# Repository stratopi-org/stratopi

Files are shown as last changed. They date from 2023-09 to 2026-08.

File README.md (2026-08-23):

# StratoPi 🎈 👽 🛸

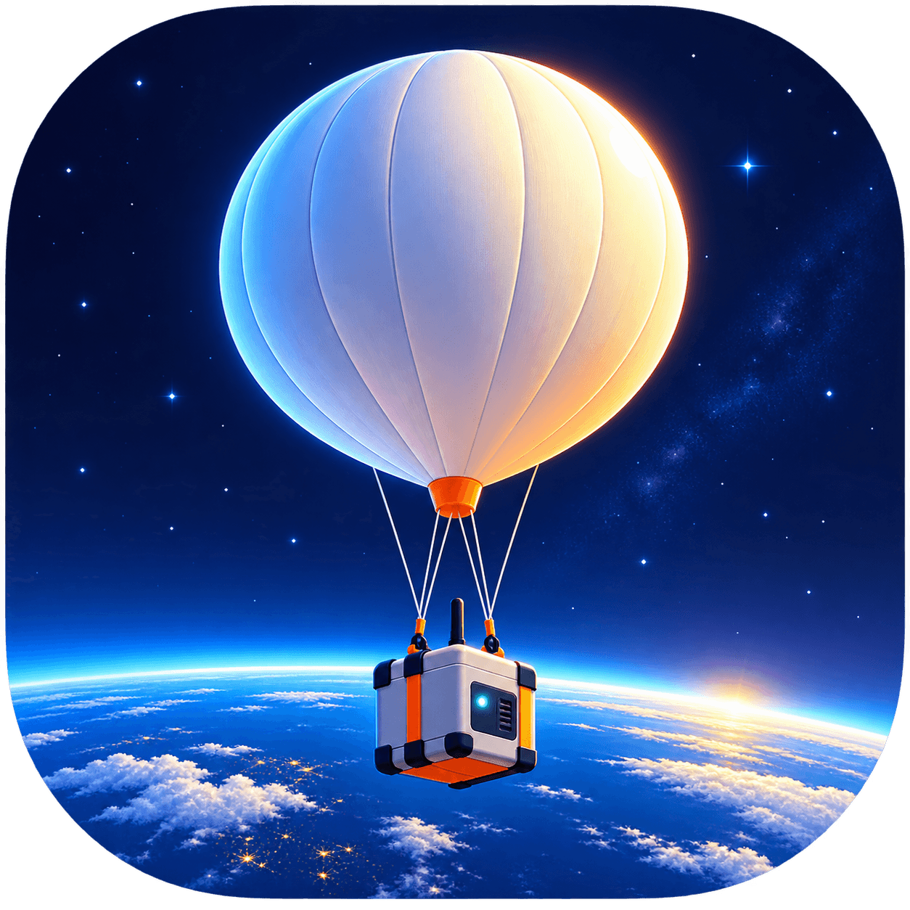
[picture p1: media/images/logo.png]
StratoPi


## Goal

The goal is to launch a latex weather balloon filled with helium into the stratosphere while recording the entire video footage of the ascent and descent flights using multiple cameras. Successfully recover the payload, which includes the Raspberry Pi computer, flight data _(date, GPS, temperature, pressure, humidity, etc)_, and video cameras and footage. If you like computing, Raspberry Pi's, space, flight, and have way too much free time, this might just be the project for you.

- Altitude goal is 100,000ft _(30,480m)_.

Open sourced and community developed. StratoPi is 100% purely a hobby project with zero financial incentives. All parts purchased at retail prices. My experience is mostly as the founder of [Elastic Byte](https://elasticbyte.net) and a DevOps Engineer so this is definitely uncharted territory for me personally.

## Parts

View the [parts list](https://github.com/stratopi-org/stratopi/blob/master/PARTS.md).

## Legality / FAA

According to the [Strato Flights website](https://www.stratoflights.com/en/tutorial/weather-balloon-registration-insurance/usa/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,FAA%20Part%20101), must have approval from the Federal Aviation Administration _(FAA)_. _Laws and regulations may undergo significant changes at any time due to ongoing developments involving spy balloons._

See:

- https://eclipse.montana.edu/education/engineering-course/eng-lesson09-faaregs.pdf
- https://www.ecfr.gov/current/title-14/chapter-I/subchapter-F/part-101
- https://www.ecfr.gov/current/title-14/chapter-I/subchapter-C/part-48
- https://www.cbsnews.com/news/military-tracking-balloon-western-us-military/

## Media

Raspberry Pi computer, battery, communications payload overview (http://www.youtube.com/watch?v=SpzycIWPKsQ "Raspberry Pi computer, battery, communications payload overview")

RunCam 5 Camera Unboxing (http://www.youtube.com/watch?v=Ua4CM7kJQfI "RunCam 5 Camera Unboxing")

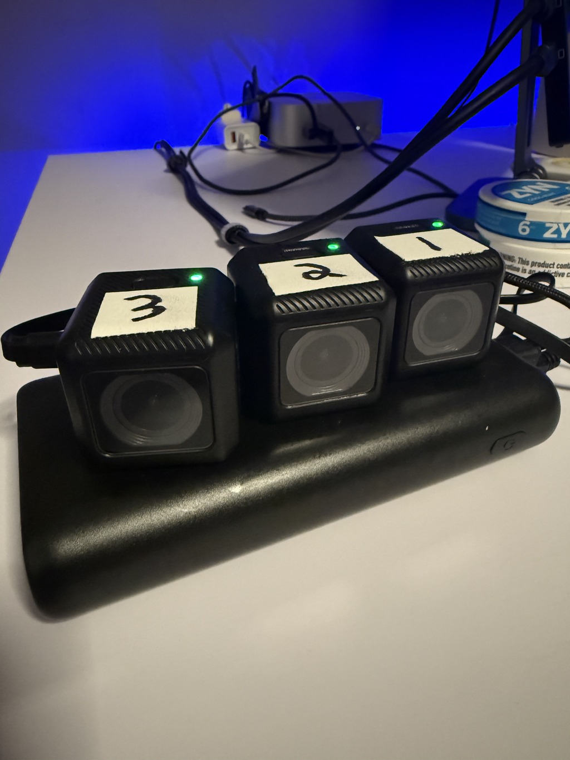
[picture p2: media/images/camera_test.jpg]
RunCam 5 Camera Power Test


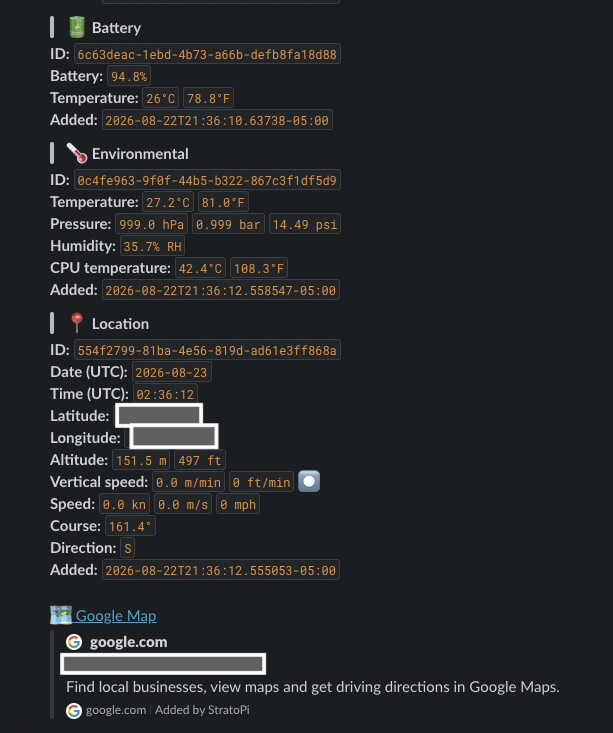
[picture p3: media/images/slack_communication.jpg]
Slack Communication


## Software architecture

All the software is written in Python 3 using standard PyPI packages. The pattern of each application is essentially poll for some data, and then insert that data into PostgreSQL. The exception being the communication application which listens for data from PostgreSQL via `pg_notify` and sends it to Slack via cellular networks. Originally, I was planning to run each application in a Docker container but decided to keep things as simple as possible and opted to use tried and true _systemd_ services for each application. [KISS](https://en.wikipedia.org/wiki/KISS_principle)!

- ### [battery](https://github.com/stratopi-org/stratopi/tree/master/software/battery)

Polls the battery percentage as well as the battery temperature and inserts the data into PostgreSQL.

- ### [communication](https://github.com/stratopi-org/stratopi/tree/master/software/communication)

Listens for battery, environmental, and location data from PostgreSQL via `pg_notify` and sends it to Slack via cellular networks.

- ### [environmental](https://github.com/stratopi-org/stratopi/tree/master/software/environmental)

Polls the Bosch BME280 sensor, Raspberry Pi CPU temperature, and inserts the data into PostgreSQL. Provides temperature, atmospheric pressure, and humidity.

- ### [location](https://github.com/stratopi-org/stratopi/tree/master/software/location)

Polls the Waveshare GPS and inserts the data into PostgreSQL. Provides date, time, latitude, longitude, altitude, speed, and course. From course, can also determine direction such as North, Southeast, etc. Addditionally vertical speed per minute is automatically calculated via a PostgreSQL trigger _(see [code](https://github.com/stratopi-org/stratopi/blob/master/software/location/database-schema.sql#L45))_.

## Tests

View [various tests](https://github.com/stratopi-org/stratopi/blob/master/docs/tests.md) _(camera, mass, power, etc)_.

## Wanna help?

- See [GitHub Issues](https://github.com/stratopi-org/stratopi/issues?q=is%3Aopen+is%3Aissue+label%3Aenhancement) for outstanding tasks
- Potentially joining the launch and recovery in person _(Tennessee launch...)_
- Code review and PR's of my _noob_ Python 🙈. Dig into the [software](https://github.com/stratopi-org/stratopi/tree/master/software).
- Parts recommendations and optimizations
- 3d modeling and printing _(structural and mounting aspects)_
- Website / Github Pages
- Flight, space, physics experience as I am sure I am negligently overlooking details
- GIS and GPS experience. KML, GeoJSON, GPS Visualizer, Google Earth/Maps
- Video editing of the flight footage 🤞
- Have a latex baloon "hookup"?
- Have a helium "hookup"? 😉

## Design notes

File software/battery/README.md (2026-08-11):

# battery

## Create PostgreSQL Schema

```shell
sudo -u postgres psql -h 127.0.0.1 -d stratopi -U stratopi -f ./database-schema.sql --password
```

## Install systemd Service

```shell
./install.sh
```

## Environment Variables

- `LOG_LEVEL` _(default=INFO)_
- `POSTGRES_URL` _(required)_

## View Logs

```shell
./logs.sh [--follow]
```

## Utilities

- Create a PostgreSQL `pg_dump` backup of battery data:

```shell
python -m util.backup
```

- Truncate all battery data from PostgreSQL:

```shell
python -m util.truncate
```

## Pip

- `pip-outdated` checks if any PyPI packages are outdated.

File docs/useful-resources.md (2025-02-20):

# Documentation and resources

- [National Weather Service Weather Balloon / Upper Air Observations](https://www.weather.gov/rev/upperair)
- [Weather Balloon Tutorial](https://www.stratoflights.com/en/tutorial/)
- [UK High Altitude Society](https://www.ukhas.org.uk/doku.php?id=start)
- [FAA Regulations for Unmanned Free Balloons](https://eclipse.montana.edu/education/engineering-course/eng-lesson09-faaregs.pdf)
- [Nationwide Eclipse Ballooning Project](https://eclipse.montana.edu/)
- [PiSugar 3 Wiki](https://github.com/PiSugar/PiSugar/wiki/PiSugar-3-Series)
- [Waveshark SIM7600E-H 4G HAT product page](https://www.waveshare.com/wiki/SIM7600E-H_4G_HAT)
- [Core Electronics - 4G and GPS HAT For Raspberry Pi - Waveshare SIM7600X](https://core-electronics.com.au/guides/raspberry-pi-4g-gps-hat/)
- [Raspberry Pi Weather Station (video)](https://www.youtube.com/watch?v=ChQpD2gsC20&ab_channel=ExplainingComputers)
- [Humidity, temperature and pressure project on RaspberryPi](https://projects.raspberrypi.org/en/projects/build-your-own-weather-station/2)
- [Using 4G LTE wireless modems on a Raspberry Pi](https://www.jeffgeerling.com/blog/2022/using-4g-lte-wireless-modems-on-raspberry-pi)
- [SIMPLEKML](https://simplekml.readthedocs.io/en/latest/gettingstarted.html)
- [SiRF NEMA Reference Manual](https://www.sparkfun.com/datasheets/GPS/NMEA%20Reference%20Manual-Rev2.1-Dec07.pdf)

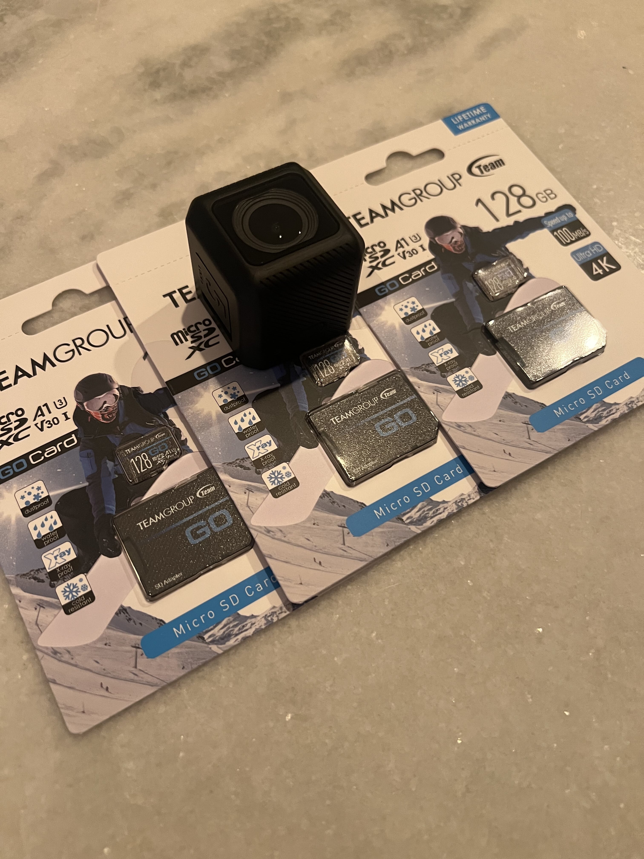
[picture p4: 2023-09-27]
media/images/runcam_5_camera_sd_cards-min.jpg

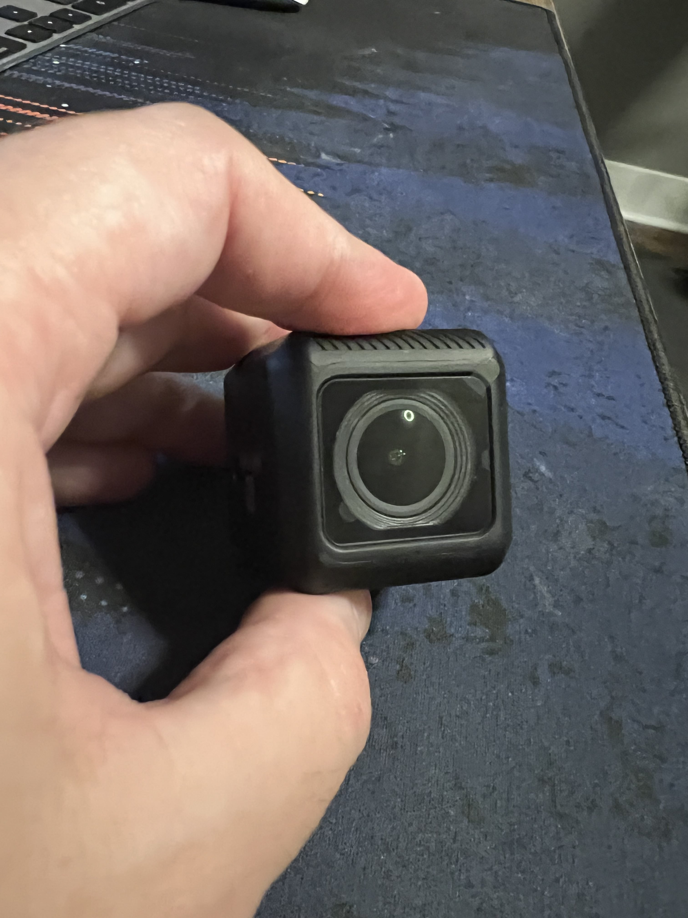
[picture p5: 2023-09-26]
media/images/runcam_5_camera_front.jpg

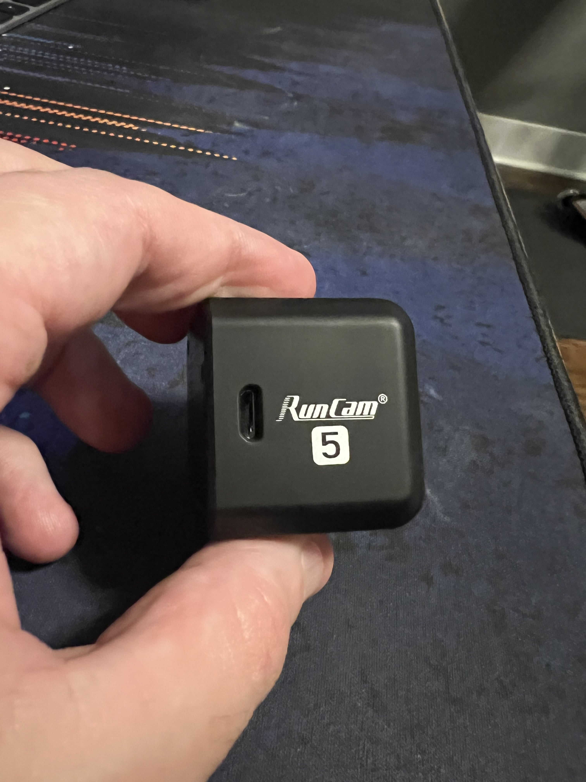
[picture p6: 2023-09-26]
media/images/runcam_5_camera_side.jpg

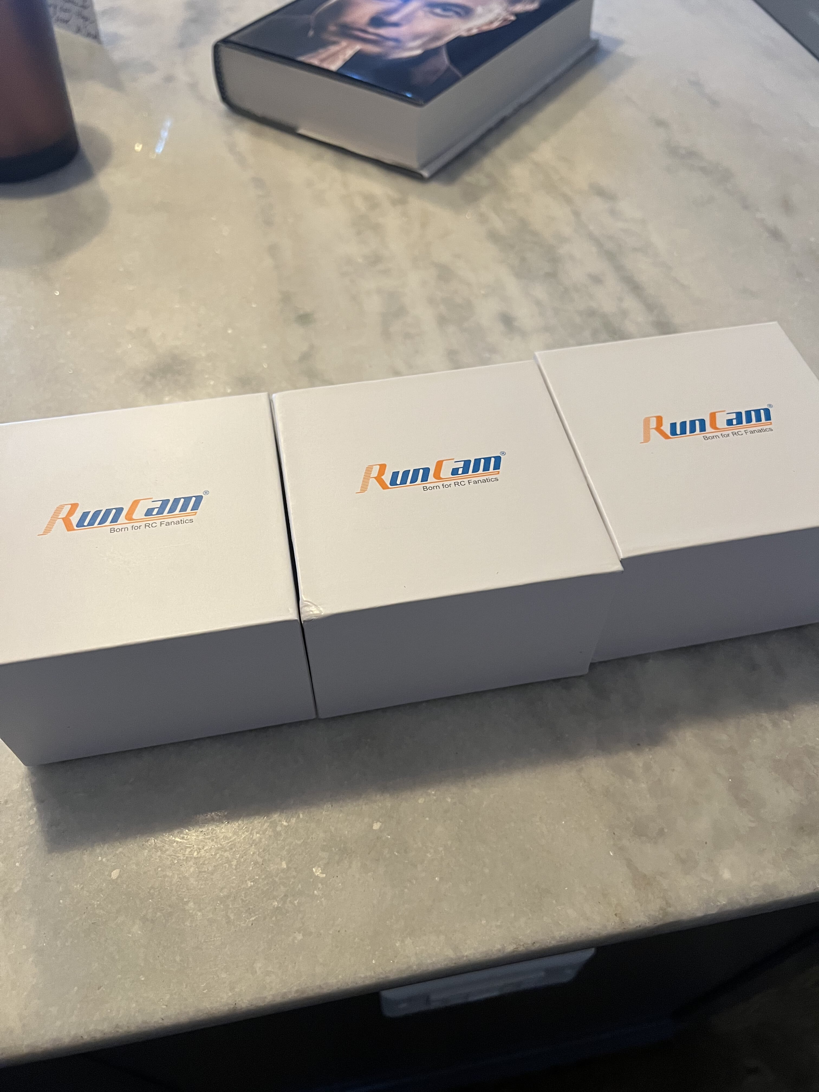
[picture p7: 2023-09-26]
media/images/runcam_5_cameras_boxed.jpg

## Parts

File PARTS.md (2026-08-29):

# Parts list

- ### Weather balloon

*(TBD)* [Latex weather balloon](https://github.com/stratopi-org/stratopi/blob/master/PARTS.md)

- ### Computer

[Raspberry Pi 3 B+](https://www.raspberrypi.com/products/raspberry-pi-3-model-b-plus/). I already had an extra Raspberry Pi 3 B+ lying around so I used that. It's plenty powerful in terms of processing and memory and it's really power efficient. A newer [Raspberry Pi 4](https://www.raspberrypi.com/products/raspberry-pi-4-model-b/) would work as well.

- ### Cameras

[RunCam 5 Orange](https://shop.runcam.com/runcam-5-orange/). Ultra-light _(56 grams)_ 4K HD camera with image stabilization. Uses a Sony IMX 377 12MP sensor and specifically built for airborne [FPV](https://en.wikipedia.org/wiki/First-person_view_\(radio_control\)).<br />
[TEAMGROUP microSD Card 128GB - 3 Pack](https://www.amazon.com/dp/B09WRFQYW3). microSD storage for video footage.

- ### Cellular communication / GPS

[Waveshare SIM7600A-H 4G HAT Board](https://www.amazon.com/gp/product/B07PLTP3M6). Provides GPS support which facilitates locating the payload after descent and communications capability using 4G cellular networking.<br />
[Simbase SIM card and connectivity](https://www.simbase.com/). Provides cellular connectivity for IOT devices using multiple mobile operators. Cellular data is *VERY* expensive _($0.01 per MB)_ with Simbase so optimizations and clever solutions need to be implemented in the communications application.

- ### Auxiliary location

[Apple AirTag](https://www.apple.com/shop/buy-airtag/airtag/1-pack). Provides auxiliary location tracking using bluetooth and the Apple Find My network.

- ### Temperature, pressure, humidity sensor

[Bosch BME280 Sensor](https://www.amazon.com/gp/product/B0BQFV883T). Provides environmental data.
I used the [ELEGOO 40pin cable pack](https://www.amazon.com/gp/product/B01EV70C78) to connect the BME280 sensor to the Raspberry Pi.

- ### Computer battery

[PiSugar 3 Plus](https://www.amazon.com/PiSugar-Plus-Pwnagotchi-Management-Raspberry/dp/B0FBK89B8H/). A integrated battery and software controller specifically designed for Raspberry Pi's.

- ### Camera battery

[RGVOTA 38800mAh USB-A power bank](https://www.amazon.com/Portable-38800mAh-Charging-External-Essential/dp/B0G1YKB8WK/). Required extended battery power for the cameras.

- ### Parachute

*(TBD)* [Parachute](https://github.com/stratopi-org/stratopi/blob/master/PARTS.md)<br />
*(TBD)* [Parachute cord / braided polyester/Dacron kite line](https://github.com/stratopi-org/stratopi/blob/master/PARTS.md)

- ### Payload / external shroud

[Owens Corning FOAMULAR NGX F-150 1 in. x 4 ft. x 8 ft. SSE R-5 XPS Rigid Foam Board Insulation](https://www.homedepot.com/pep/Owens-Corning-FOAMULAR-NGX-F-150-1-in-x-4-ft-x-8-ft-SSE-R-5-XPS-Rigid-Foam-Board-Insulation-20WENGX/315197840)<br />
[3/8 in. X 3/16 in. X 10 ft. Black High-Density Rubber Foam Weatherstrip Tape](https://www.homedepot.com/pep/Frost-King-3-8-in-X-3-16-in-X-10-ft-Black-High-Density-Rubber-Foam-Weatherstrip-Tape-R338H/100197882)<br />
[PL 300 Foamboard 10 oz. Latex Construction Adhesive](https://www.homedepot.com/pep/Loctite-PL-300-Foamboard-10-oz-Latex-Construction-Adhesive-Blue-Cartridge-1421941/202020476)<br />
[JB Weld Plastic Bonder Epoxy](https://www.homedepot.com/p/J-B-Weld-0-85-oz-Plastic-Bonder-Epoxy-50133H/303710788)<br />
[Scotch Bi-Directional Filament Tape 8959 Transparent](https://www.amazon.com/gp/product/B00006XY3H)<br />
[3M Multi-Use Colored Duct Tape, Orange with Strong Adhesive and Water-Resistant Backing](https://www.amazon.com/3M-Multi-Use-Adhesive-Water-Resistant-Multi-Surface/dp/B073WKYJ5K)<br />
[HUASAI 4/5" 100 Pack Zip Tie Mount](https://www.amazon.com/dp/B07Z79LHJC)

- ### FAA requirements, and miscellaneous

*(TBD)* [Lighting / strobes / beacons](https://github.com/stratopi-org/stratopi/blob/master/PARTS.md)<br />
*(TBD)* [Radar reflector](https://github.com/stratopi-org/stratopi/blob/master/PARTS.md)

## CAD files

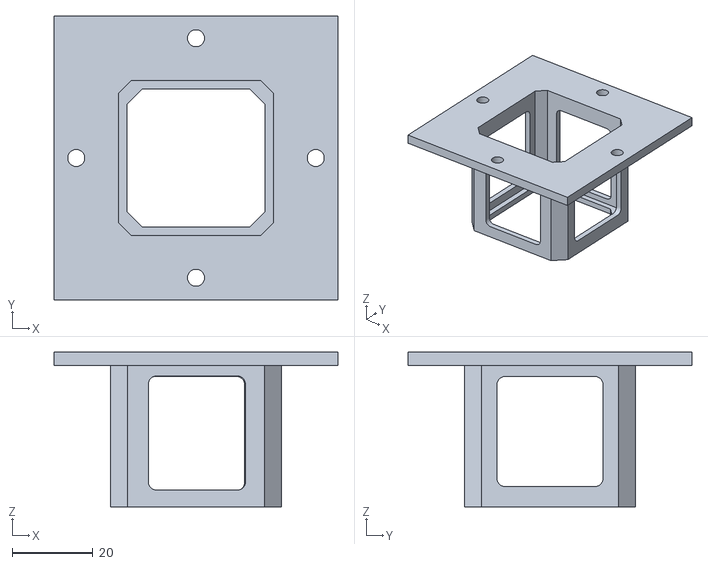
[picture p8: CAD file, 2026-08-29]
media/3d/runcam5-orange-mount.stl
70.2 x 70.2 x 38.2

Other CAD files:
media/3d/runcam5-orange-mount-fillet.stl

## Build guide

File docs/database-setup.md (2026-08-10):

# Database

- PostgreSQL 15 on [Pi OS](https://www.raspberrypi.com/software/)

## Install

```shell
sudo apt-get install -y --no-install-recommends gcc lsb-release gnupg2
```

```shel
echo "deb http://apt.postgresql.org/pub/repos/apt/ $(lsb_release -cs)-pgdg main" | sudo tee /etc/apt/sources.list.d/pgdg.list
curl -sSL https://www.postgresql.org/media/keys/ACCC4CF8.asc | sudo apt-key add -
sudo apt-get update
sudo apt-get install -y --no-install-recommends libc-dev libpq-dev postgresql-15 postgresql-client-15
sudo apt-get -y autoremove
sudo apt-get clean
```

## Setup

Create the StratoPi PostgreSQL user.

```shell
sudo su - postgres
createuser --interactive --pwprompt
```

Create the StratoPi PostgreSQL database.

```shell
sudo su - postgres
createdb stratopi --owner=stratopi
```

Grant PostgreSQL privileges.

```shell
sudo su - postgres
psql -d stratopi
GRANT ALL PRIVILEGES ON DATABASE stratopi TO stratopi;
```

Adjust PostgreSQL host-based authentication. Append to file `/etc/postgresql/15/main/pg_hba.conf`:

```
local   stratopi        stratopi                                trust
host    stratopi        stratopi        127.0.0.1/32            trust
host    stratopi        stratopi        10.0.0.1/22             trust
```

*NOTE:* You likely will not need to add `10.0.0.1/22`. I've added that subnet so I can use remote database GUIs on my local home network.

```shell
sudo service postgresql restart
```

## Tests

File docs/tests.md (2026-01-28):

# January 28th 2026

### Masses

- _(3x)_ RunCam 5 Oranges and the RGVOTA 38800mAh USB-A power bank: `634g`

# January 27th 2026

### Camera and USB-A battery test

- Upon running _(3x)_ RunCam 5 Oranges powered by the RGVOTA 38800mAh USB-A power bank lasted for `7 hours and 28 minutes`. Each camera video resolution was set to `2.7k@60fps`, with recording duration limited by the 128GB microSD card storage capacity.

    - Storage used: `111GB` each camera
    - USB-A power bank percentage remaining when storage was filled: `N/A%`
    - Ambient temperature: `18.3°C / 65°F`

# February 12th 2025

### Masses

- Raspberry Pi 3 B+, PiSugar 3 Plus, Waveshare SIM7600A-H 4G HAT Board, and Bosch BME280 Sensor: `266g`

# February 24th 2024

### Computer battery test

- Upon running [battery](https://github.com/stratopi-org/stratopi/tree/master/software/battery), [environmental](https://github.com/stratopi-org/stratopi/tree/master/software/environmental), and [location](https://github.com/stratopi-org/stratopi/tree/master/software/location) for 1 hour, the PiSugar 3 Plus battery level decreased from `100%` to `91.1%`, indicating a drain of `8.9%` per hour and suggesting an estimated total battery life of approximately `11 hours`.

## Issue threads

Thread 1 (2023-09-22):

Raspberry Pi date/time incorrect without internet on boot (no RTC)

nodesocket, 2023-09-22:
Raspberry Pi date and time will be incorrect if booted without an active internet connection because it cannot connect to NTP and there is no real-time clock on the Pi. However, the GPS date and time fields should be correct in [location](https://github.com/stratopi-org/stratopi/tree/master/software/location).

nodesocket, 2024-02-22:
Correction, there is a RTC on the PiSugar 3 Plus. See the Wiki at https://github.com/PiSugar/PiSugar/wiki/PiSugar-3-Series#rtc-on-board how to setup and use the RTC.

Closed 2024-02-22.

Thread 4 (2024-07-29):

Implement vertical speed

nodesocket, 2024-07-29:
Implement [vertical speed](https://en.wikipedia.org/wiki/Rate_of_climb) _(m/min and ft/m)_ into the location app. Use altitude deltas and time to calculate vertical speed.

nodesocket, 2025-02-13:
Chat GPT gives the following math from altitude and date to calculate acceleration and related to vertical speed. 🧠

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

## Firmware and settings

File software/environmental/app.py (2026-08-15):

import argparse
import asyncio
import os
import time

import bme280
import psycopg2
import smbus2
from lib import common, log, pi

NAME = 'environmental'
SLEEP_TIME = 60 * 1   # 1 minute
BME280_ADDRESS = 0x76

try:
    with open('.version', 'r', encoding='UTF-8') as f:
        VERSION = f.read().strip()
except FileNotFoundError as err:
    log.error(err, exit_code=3)


parser = argparse.ArgumentParser(prog=NAME)
parser.add_argument('--version',
                    action='version',
                    version=f'{NAME} v{VERSION} ({common.python_version()})',
                    help='show version and exit')

parser.parse_args()

log.info(f'{NAME} v{VERSION} ({common.python_version()})')
log.info(f'refreshing {NAME} data every {common.sec_to_min(SLEEP_TIME)} minute(s)')

bus = smbus2.SMBus(1)

max_attempts = 5
for attempt in range(1, max_attempts + 1):
    try:
        calibration_params = bme280.load_calibration_params(
            bus,
            BME280_ADDRESS,
        )
        break
    except OSError as err:
        if attempt == max_attempts:
            raise

        log.warning(
            f'failed to initialize BME280 '
            f'(attempt {attempt}/{max_attempts}): {err}; retrying...'
        )

        time.sleep(2)


async def loop_fn():
    while True:
        conn = psycopg2.connect(os.environ['POSTGRES_URL'])
        masked_postgres_url = common.mask_postgres_url_password(
            os.environ['POSTGRES_URL'])
        log.debug(f'connected to PostgreSQL ({masked_postgres_url})')

        cursor = conn.cursor()

        try:
            data = bme280.sample(bus, BME280_ADDRESS, calibration_params)
            temperature = common.format_data(data.temperature)
            pressure = common.format_data(data.pressure)
            humidity = common.format_data(data.humidity)
            cpu_temperature = pi.get_cpu_temperature()

            cursor.execute('INSERT INTO environmental (temperature_c, pressure_hpa, humidity_rh, cpu_temperature_c) VALUES (%s, %s, %s, %s)',
                           (temperature, pressure, humidity, cpu_temperature))

            conn.commit()
            log.info(
                f'inserted {NAME} data temp={temperature}°C, pressure={pressure} hPa, humidity={humidity}% RH, cpu_temp={cpu_temperature}°C into PostgreSQL')
        except Exception as err:
            conn.rollback()
            log.error(err)
        finally:
            cursor.close()
            conn.close()
            log.debug('closed PostgreSQL connection')

        await asyncio.sleep(SLEEP_TIME)

asyncio.run(loop_fn())

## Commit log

2023-08-16 added battery to software
2023-08-17 early version of battery software
2023-08-17 utils => util. boilerplate app.py in battery
2023-08-18 adds database software README.md. improves battery backup util
2023-08-18 remove docker from battery software
2023-08-18 updated battery software README.md
2023-08-18 fix typo in battery lib common.py
2023-08-18 fix battery app.py
2023-08-18 attempting to read temperature
2023-08-18 use log lib in battery software
2023-08-18 battery software tweaks
2023-08-18 updated battery README.md
2023-08-19 battery v0.2.0
2023-08-19 add asyncio to battery
2023-08-19 log when connected to unix socket
2023-08-19 fix bug in battery
    [app.py]
2023-08-19 initialize socket_client in battery
2023-08-19 integrate most of PostgreSQL into battery
2023-08-20 adds battery database-schema.sql and logic to insert into PostgreSQL
2023-08-20 fix inserting into PostgreSQL
    [app.py]
2023-08-20 improved battery
2023-08-20 fix trim() to strip()
    [app.py]
2023-08-26 fetch/store voltage and current in battery
2023-08-26 adjust battery database schema
2023-08-26 add str_format option to battery common cleanup_data
2023-08-26 working version of battery hopefully
2023-08-26 wizardly to fix socket data
2023-08-26 remove battery voltage and current
2023-08-26 optimization in unix socket
2023-08-26 add strip() to unix socket lib
2023-08-29 break apart battery unix sends
2023-08-29 updated unix socket function
2023-08-29 more debugging of unix socket
2023-08-29 revert to simplier version of unix socket send
2023-08-29 revert unix socket
2023-08-29 unix socket debugging
2023-08-30 more optimization in battery app
2023-08-30 optimizations in unix socket
2023-08-30 fix bug in unix socket close()
2023-08-30 close unix sockets immediately in battery
2023-08-30 better logic in close() for unix socket
2023-08-30 updated unix socket
2023-08-30 run strip() on unix socket response after split
2023-08-30 adjust receive_buffer to 1024 in unix socket
2023-08-30 strip out long from unix socket responses
2023-08-30 hopefully fix replace issue in unix socket
2023-08-30 improved unix socket function
2023-08-30 strip newlines from debug messages in unix socket
2023-08-30 optimize unix socket
2023-08-30 battery loop 3 minutes instead of 2
2023-08-30 correct parse function in gps
    [app.py]
2023-08-30 fix bug in location gps
    [app.py]
2023-08-31 improved output from battery
2023-08-31 minor updates to battery
2023-08-31 adds stall-service.sh for battery
2023-08-31 fixed install-service.sh for battery
2023-08-31 fix battery install-service.sh
2023-08-31 fix battery install.sh
2023-08-31 rename column temperature to temperature_c
2023-09-05 bump version of battery
2023-09-05 appended After=postgresql.service to battery install service
2023-09-05 improved battery install script
2023-09-05 updated battery install script
2023-09-07 add battery truncate util script
2023-09-07 insert location into database
2023-09-07 bug fixes in location
    [app.py]
2023-09-07 fix referencing dict props
    [app.py]
2023-09-07 fix syntax error in location
    [app.py]
2023-09-08 fix bug in location
    [app.py]
2023-09-08 match format of numerics being inserted into PostgreSQL
2023-09-12 better error handling in location
    [app.py]
2023-09-12 attempting to fix gps
    [app.py]
2023-09-13 speed is in knots not meters per second
2023-09-19 switch to After=multi-user.target in systemd services
2023-09-26 add runcam 5 camera unboxing video
2023-09-26 add runcam 5 camera image
2023-10-03 early stage scaffolding for environmental app
2024-02-24 insert environmental data into PostgreSQL
2024-05-09 fix syntax error in location app
    [app.py]
2024-06-14 update to battery software
2024-07-03 fix order of latitude and longitude in location
    [app.py]
2024-07-03 fix order of latitude and longitude when insterting into PostgreSQL
    [app.py]
2025-02-12 add camera_teset image
2025-02-13 updated camera test image
2025-03-20 fix ordering on sql failures
    [app.py]
2026-01-27 bump all requirements to latest and optimization in battery
2026-01-27 fix battery sockets
